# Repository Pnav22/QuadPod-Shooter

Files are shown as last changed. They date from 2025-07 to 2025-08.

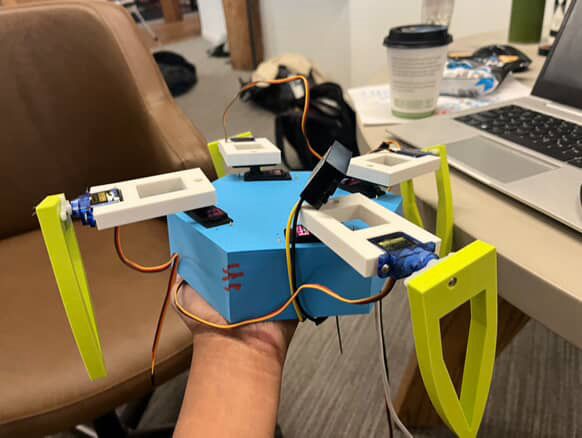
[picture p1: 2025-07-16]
Pictures/WhatsApp Image 2025-07-16 at 11.27.03_aa79fecd.jpg

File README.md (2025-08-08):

# Quadrapod Turret

**Quadrapod Turret** is a four-legged spider-bot equipped with a turret, created for the Hack Club Undercity Hackathon at github. Each leg has two servo motors that enable rotation across two axes, allowing the robot to walk smoothly. The turret features an automatic reloading and firing system. The entire robot is controlled wirelessly via Bluetooth using an Xbox controller.

## Demo Video
 [Watch it here on YouTube](https://www.youtube.com/shorts/YrqL98bALRE)

## Build Journal
We thought we needed a journal even though we didn't, so we made one. Check out our full build log in [`journal.md`](https://github.com/Pnav22/QuadPod-Shooter/blob/main/Journal.md)   

Check out some more pictures in [`Pictures`](https://github.com/Pnav22/QuadPod-Shooter/tree/main/Pictures)

**Creators:** Joel Biswas, Ayush Jaiswal, and Pranav Mukkara

CAD                         |  IRL
:-------------------------:|:-------------------------:
CAD Render  |  IRL Build

---

## Movement Mechanism

The robot has four legs, each with two joints controlled by servo motors:

- **MG996R servo**: Controls one joint axis  
- **SG90 servo**: Controls the other joint axis

Together, these allow each leg to move in two degrees of freedom, enabling the robot to walk with stability and precision.

---

## Turret Mechanism

- Two **N20 DC motors** power the flywheels that launch ammunition.  
- An **SG90 servo motor** controls the reloading mechanism.  
- Ammunition consists of 1 cm spherical pellets loaded in a vertical tube.  
- The servo pushes ammo into the flywheels, which spin at high speed to fire the pellets.

---

## Design

Cad can be viewed [here](https://cad.onshape.com/documents/1f07b48c7f0c844885f208f0/w/35ef43929f689d5c59df734c/e/4c060ffb7e05090ceb09d7bd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).

SpiderCAD

Read Journal.md to see our engineering process!
---

## Bill of Materials

| Item | Quantity |
|---|---|
| SG90 Servo Motor | 5 |
| MG996R Servo | 5 |
| ESP32 DevKit C | 1 |
| Breadboard | 1 |
| Male to Male Jumper Wires | 30 |
| 3S LiPo Battery | 1 |
| 12V to 5V Buck Converter | 1 |
| PLA (kgs) | 1 |
| N20 Motor | 2 |
| XT60 Male Connector | 1 |

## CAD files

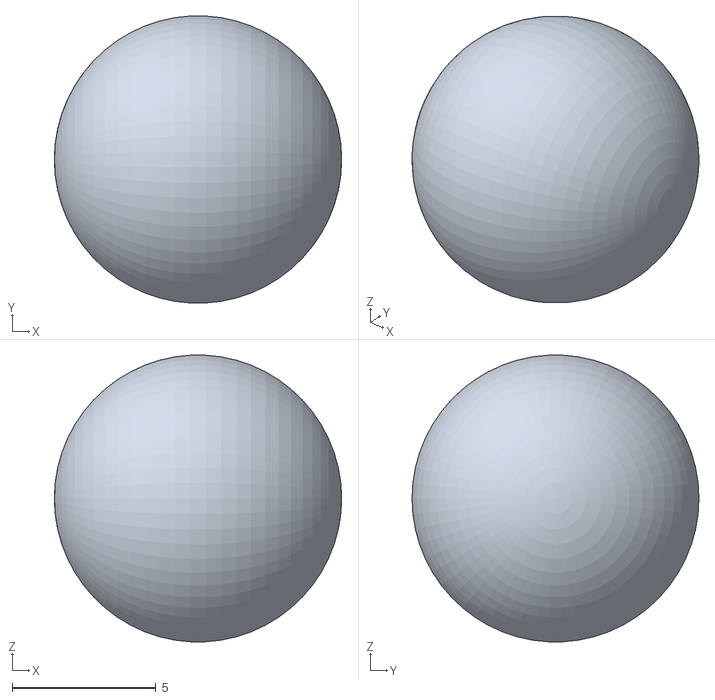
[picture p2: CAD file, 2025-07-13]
CAD/STL Files/Ammo.stl
10.0 x 9.99 x 9.97

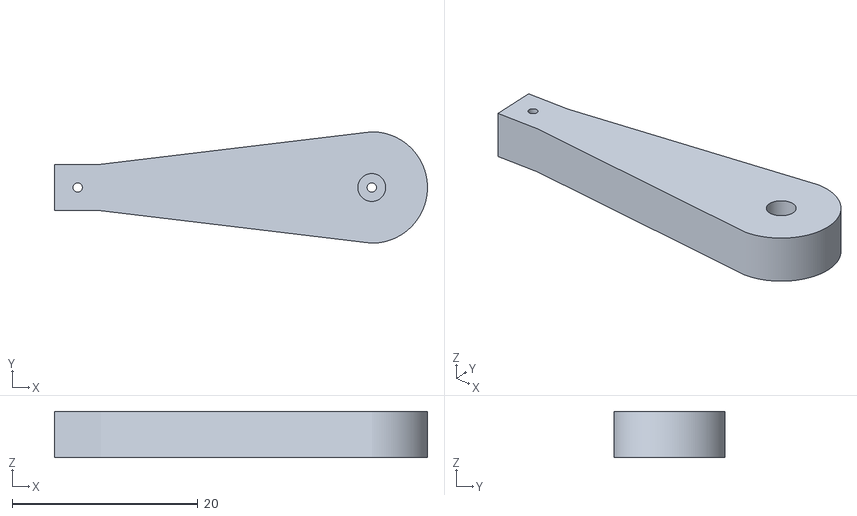
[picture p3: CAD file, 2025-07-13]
CAD/STL Files/Reload Arm.stl
40.2 x 12.0 x 5.00

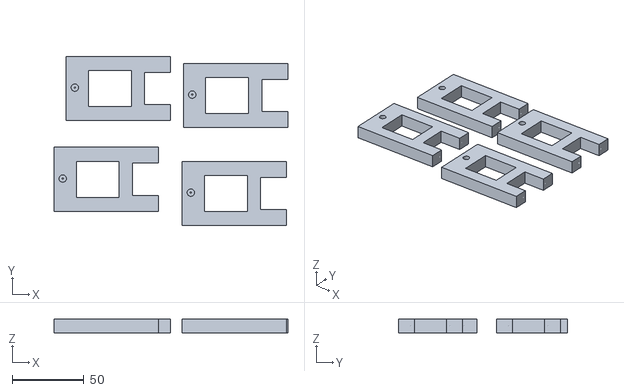
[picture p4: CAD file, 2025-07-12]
Production/legs.stl
163.4 x 118.3 x 10.0

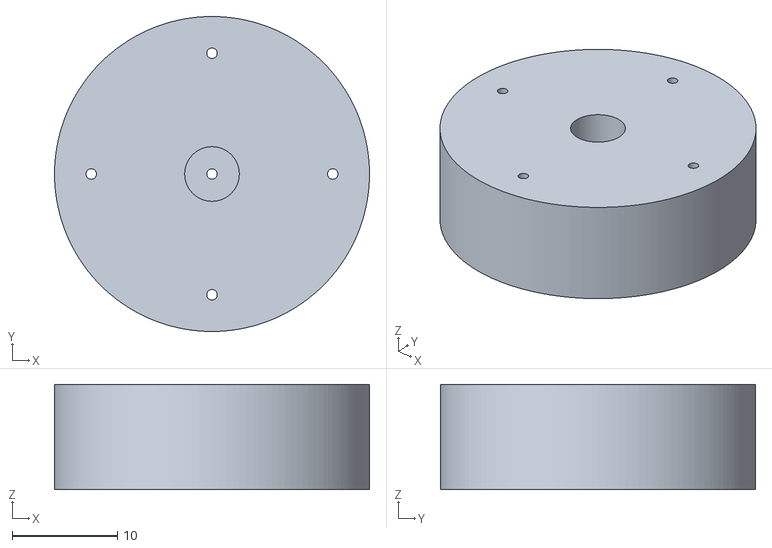
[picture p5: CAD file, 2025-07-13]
CAD/STL Files/Reload Wheel.stl
30.0 x 30.0 x 10.0

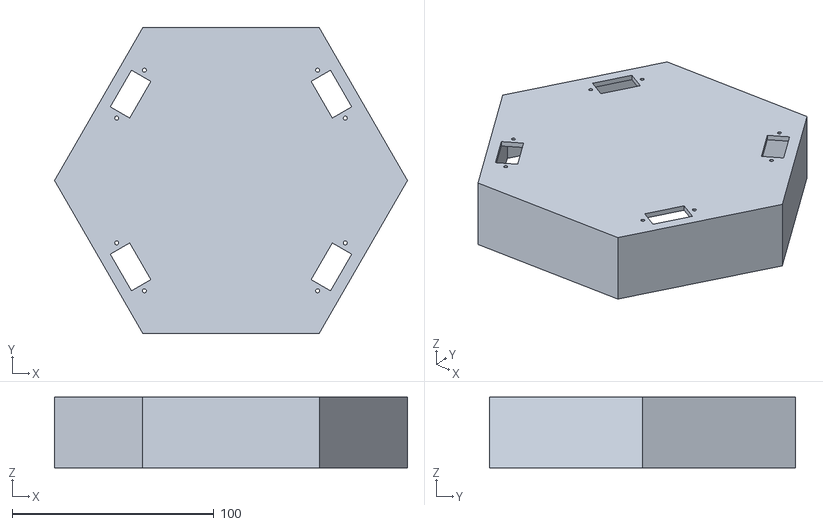
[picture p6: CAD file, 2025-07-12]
Production/Body.stl
175.0 x 151.6 x 35.0

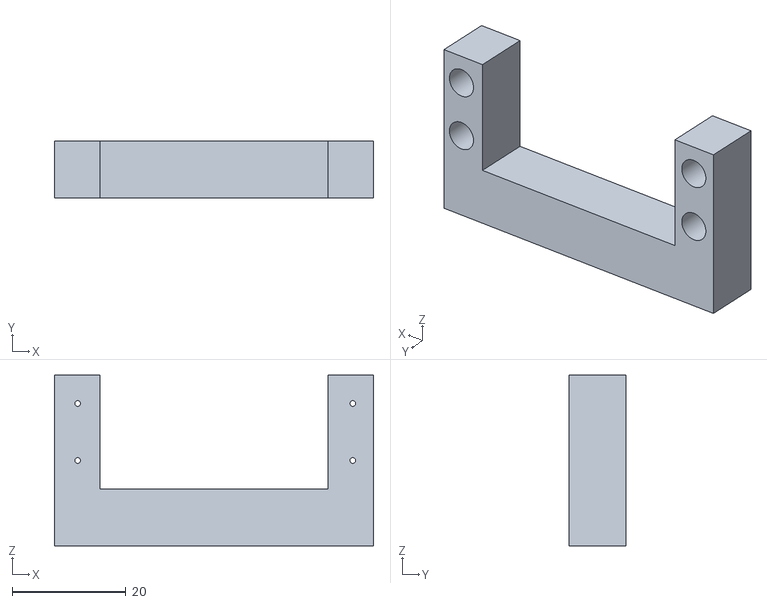
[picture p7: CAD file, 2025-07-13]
CAD/STL Files/Turret Mounting Bracket.stl
56.0 x 10.0 x 30.0

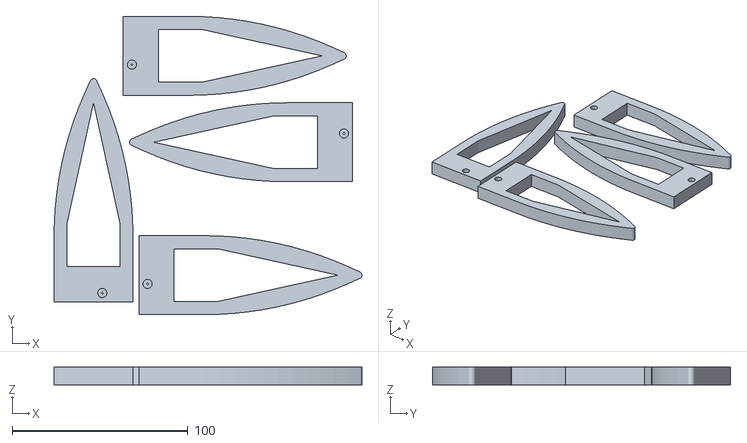
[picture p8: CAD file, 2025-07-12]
Production/claws.stl
175.4 x 169.9 x 10.0

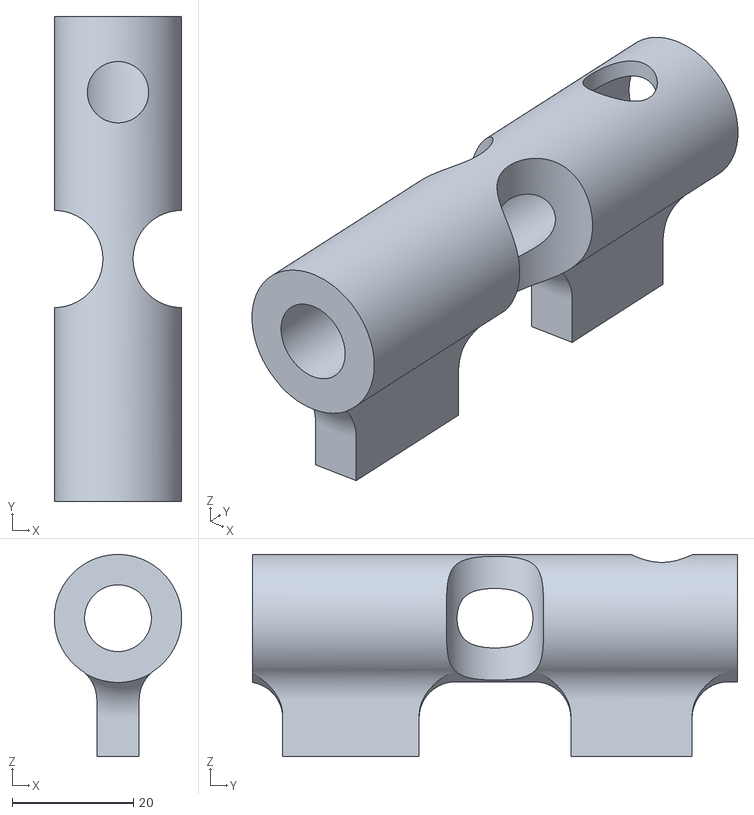
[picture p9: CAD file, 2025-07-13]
CAD/STL Files/Shaft.stl
21.0 x 80.0 x 33.3

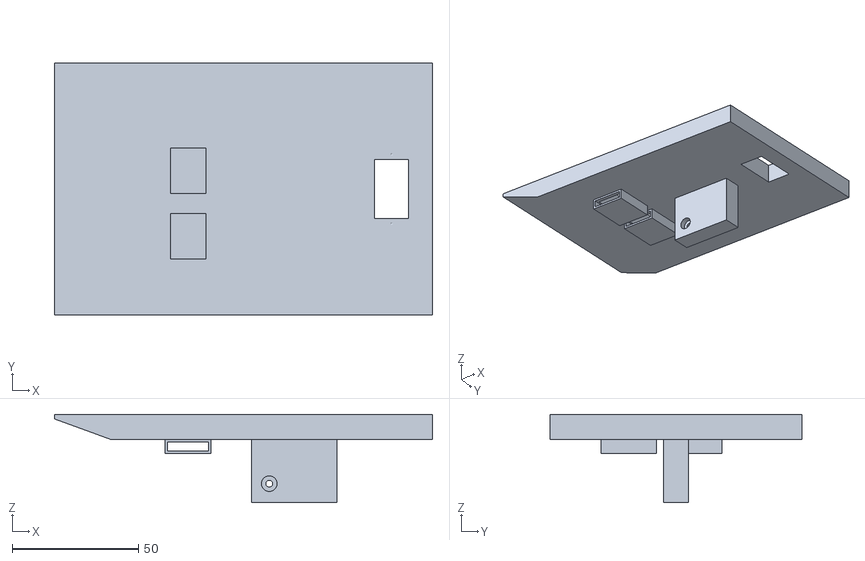
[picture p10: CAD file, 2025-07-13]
CAD/STL Files/Baseplate.stl
150.0 x 100.0 x 35.0

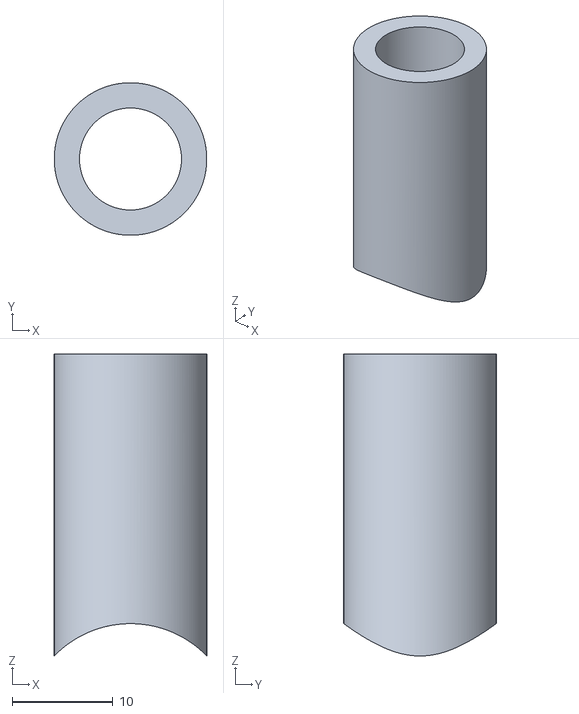
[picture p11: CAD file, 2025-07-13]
CAD/STL Files/Chamber.stl
15.1 x 15.1 x 29.9

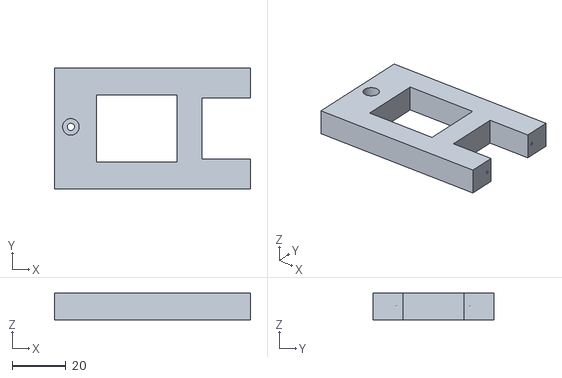
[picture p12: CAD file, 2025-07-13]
CAD/STL Files/Leg X Axis.stl
73.0 x 45.0 x 10.0

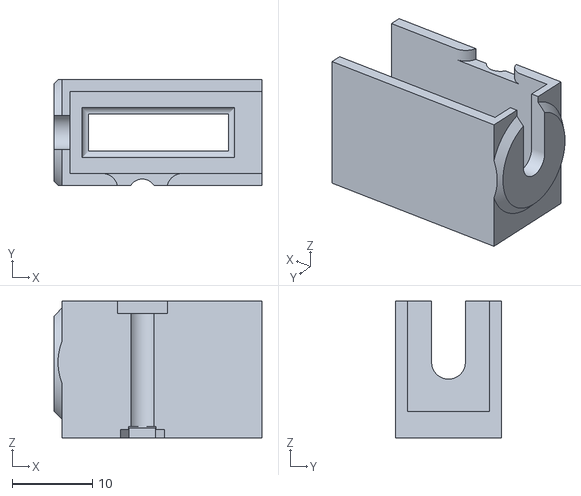
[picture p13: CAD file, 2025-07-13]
CAD/STL Files/Motor Mounts.stl
25.9 x 13.2 x 17.0

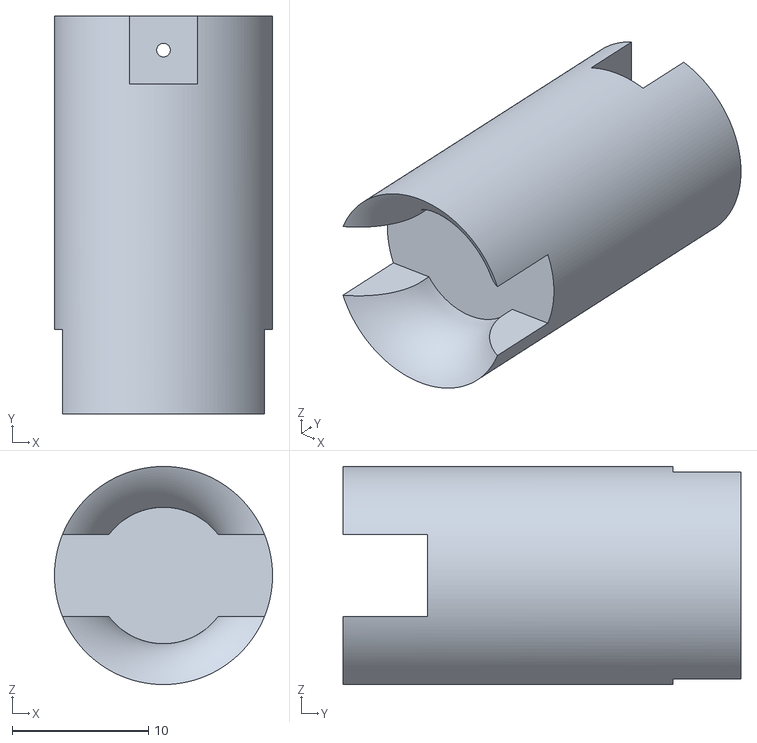
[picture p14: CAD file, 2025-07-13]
CAD/STL Files/Pusher.stl
16.0 x 29.2 x 16.0

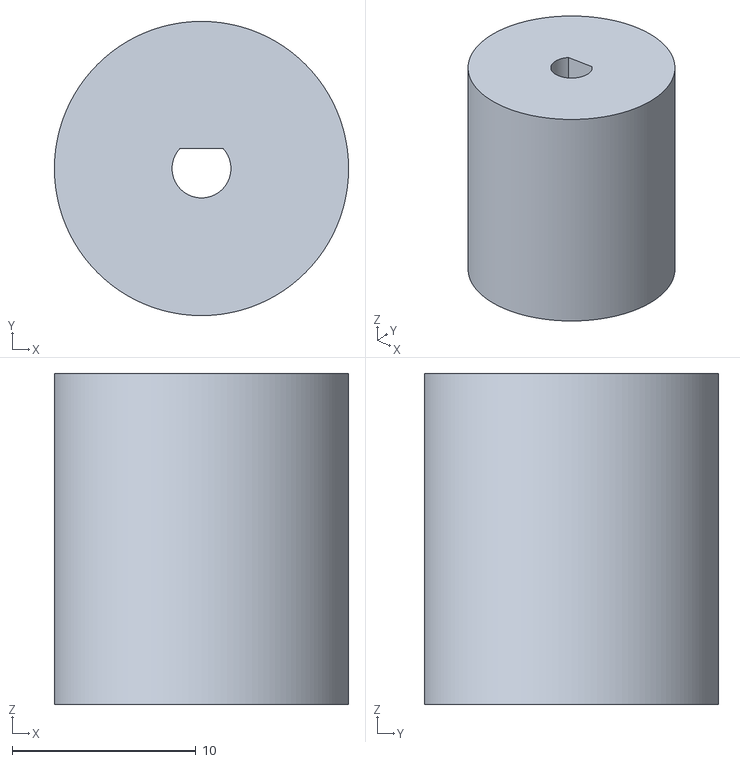
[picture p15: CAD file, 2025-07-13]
CAD/STL Files/Flywheel.stl
16.0 x 16.0 x 18.0

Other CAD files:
Production/Turret.gcode.3mf
CAD/STL Files/Leg Y Axis.stl

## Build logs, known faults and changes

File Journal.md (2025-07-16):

---
title: "QuadPod"
author: "Joel Biswas, Ayush Jaiswal, Pranav Mukkara"
description: "4-Leg Spider Robot"
created_at: "2025-07-11"
---

# QuadPod Build Log

## July 11: Excitement and Exploration

We just arrived at GitHub HQ. The place is amazing—tons of snacks and awesome working spaces. We're super excited to spend the next few nights here for the hackathon.

## July 11: Research and Ideas

We started brainstorming project ideas. One of our first concepts was a drone that acts like a hat—something like this:

Drone Hat Concept

Except this one would actually fly.

Then we explored the idea of a Mark Rober-style hat:

Mark Rober Hat Inspiration

We liked this, but kept brainstorming.

Eventually, we landed on the idea of a six-legged spider robot—something that would make people say, *"That's cool as f***." We found inspiration in this:

Spider Bot Inspiration

To make it even cooler, we decided to mount a Nerf gun on top.

In the end, we scaled it down to four legs to simplify the build.

## July 11 to 12: Getting Started

We began CAD work and created some basic designs:

Initial CAD Progress

We sent the parts out to get printed. One of our biggest mistakes was spending too much time on CAD before securing the parts we needed. By the time we went to grab motors, most were already gone—we were two short.

This was our first major roadblock. We didn’t check part availability before designing. Someone had taken eight of the motors we needed.

We decided to redesign the CAD to work with the motors that were still available.

Eventually, we found the original motors again and reverted to our original CAD design. Shoutout to Alex for coming in clutch with two extra motors from a workshop!





## July 12: Setting Up the ESP32

Pranav stayed up all night trying to get the ESP32 to work. He wanted to start coding but realized the board wasn’t responding.

He tried multiple computers and ESP32s, only to discover hours later that none of the USB cables he had supported data transfer. A whole all-nighter wasted.



The pin guide was also a nightmare. This was our second major roadblock. One person spent the entire night trying to set up the ESP32, only to realize none of the wires available could transfer data.

## July 12: Finalizing the CAD

We finalized the CAD and started printing and assembling. We used screws from the servo motor kits for assembly. Parts were printed and things started coming together.

## July 12: Third Roadblock - Servo Mounting

We messed up the leg brackets. The rectangular mounts that hold the servos had incorrect tolerances—the screws didn’t reach far enough. The servos weren't properly meshed with the arms, so nothing moved when powered.

To fix this, we used a soldering iron to heat-set the screws into the plastic. That way, when the servo moved, the arms moved with it.

## July 13: Fourth Roadblock - Wiring

Wiring was a nightmare. We were up at 4 a.m. redoing all the connections due to GPIO issues. Here’s a photo of the chaos:

WhatsApp Image 2025-07-13 at 15 31 15_a4ac9f2a

## July 13: Assembly

We assembled the entire robot! Here are some photos:

WhatsApp Image 2025-07-13 at 15 06 22_39daa7c8  
WhatsApp Image 2025-07-13 at 15 06 22_d549f691

The team in action:

WhatsApp Image 2025-07-13 at 15 06 22_2a913bad

## July 13: Coding

We're now deep into coding.
## July 14: Event End

This hackathon has ended so we are not working on the project anymore. We had lots of fun!

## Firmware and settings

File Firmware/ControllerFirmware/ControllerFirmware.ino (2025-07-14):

#include <Bluepad32.h>

// Servo objects
constexpr uint8_t legXPin1 = 13; // D13 - X BACK LEFT
constexpr uint8_t legXPin2 = 27; // D27 - X FRONT RIGHT
constexpr uint8_t legXPin3 = 12; // D12 - X BACK RIGHT
constexpr uint8_t legXPin4 = 14; // D14 - X FRONT LEFT

constexpr uint8_t legXChannel1 = 0;
constexpr uint8_t legXChannel2 = 1;
constexpr uint8_t legXChannel3 = 2;
constexpr uint8_t legXChannel4 = 3;

constexpr uint8_t legYPin1 = 26; // D26 - Y BACK LEFT
constexpr uint8_t legYPin2 = 32; // D32 - Y FRONT RIGHT
constexpr uint8_t legYPin3 = 25; // D25 - Y BACK RIGHT
constexpr uint8_t legYPin4 = 33; // D33 - Y FRONT LEFT

constexpr uint8_t legYChannel1 = 4;
constexpr uint8_t legYChannel2 = 5;
constexpr uint8_t legYChannel3 = 6;
constexpr uint8_t legYChannel4 = 7;

// Constants
const int neutral = 90;    // reset position
const int stepAngle = 60;  // how far forward to move
const int moveDelay = 500; // wait time between movements
const int swingAngle = 40;

const int HERTZ = 50;
const uint8_t BYTES = 12;

bool isWalking;

constexpr uint8_t STATUS_LED = 2;
ControllerPtr myControllers[BP32_MAX_GAMEPADS];

void onConnectedController(ControllerPtr ctl)
{
    Serial.println("Controller connected");
    myControllers[0] = ctl;
    digitalWrite(STATUS_LED, HIGH);
    ctl->playDualRumble(0, 500, 255, 128);
}

void onDisconnectedController(ControllerPtr)
{
    Serial.println("Controller disconnected");
    myControllers[0] = nullptr;
    digitalWrite(STATUS_LED, LOW);
}

void processGamepad(ControllerPtr ctl)
{
    if (ctl->a())
    {
        Serial.println("Rick Ross Mongolian Throat Singing");
        Serial.println(isWalking);
        if (!isWalking)
        {
          isWalking = true;
          walk();
        }
    }
}

void setup()
{
    Serial.begin(115200);

    pinMode(STATUS_LED, OUTPUT);
    digitalWrite(STATUS_LED, LOW);

    ledcSetup(legXChannel1, HERTZ, BYTES);
    ledcSetup(legXChannel2, HERTZ, BYTES);
    ledcSetup(legXChannel3, HERTZ, BYTES);
    ledcSetup(legXChannel4, HERTZ, BYTES);

    ledcSetup(legYChannel1, HERTZ, BYTES);
    ledcSetup(legYChannel2, HERTZ, BYTES);
    ledcSetup(legYChannel3, HERTZ, BYTES);
    ledcSetup(legYChannel4, HERTZ, BYTES);

    ledcAttachPin(legXPin1, legXChannel1);
    ledcAttachPin(legXPin2, legXChannel2);
    ledcAttachPin(legXPin3, legXChannel3);
    ledcAttachPin(legXPin4, legXChannel4);

    ledcAttachPin(legYPin1, legYChannel1);
    ledcAttachPin(legYPin2, legYChannel2);
    ledcAttachPin(legYPin3, legYChannel3);
    ledcAttachPin(legYPin4, legYChannel4);

    // All start at neutral position
    writeToServo(legXChannel1, neutral);
    writeToServo(legXChannel2, neutral);
    writeToServo(legXChannel3, neutral);
    writeToServo(legXChannel4, neutral);

    writeToServo(legYChannel1, neutral);
    writeToServo(legYChannel2, neutral);
    writeToServo(legYChannel3, neutral);
    writeToServo(legYChannel4, neutral);
    delay(500);

    isWalking = false;

    BP32.setup(&onConnectedController, &onDisconnectedController);
    // BP32.forgetBluetoothKeys(); PLEASE DO NOT UNCOMMENT THIS
    BP32.enableVirtualDevice(false);
}

void loop()
{
    if (BP32.update())
    {
        ControllerPtr ctl = myControllers[0];
        if (ctl && ctl->isConnected() && ctl->hasData() && ctl->isGamepad())
            processGamepad(ctl);
    }
    delay(10);
}

void writeToServo(int pwmChannel, int angle)
{
    // Map angle (0–180) to pulse width in microseconds (1000–2000)
    int us = map(angle, 0, 180, 1000, 2000);

    // Convert microseconds to duty (out of 2^16 for 16-bit resolution and 50Hz)
    uint32_t duty = (us * 4095UL) / 20000UL; // for 12-bit

    Serial.print("Angle: ");
    Serial.print(angle);
    Serial.print(" → Duty: ");
    Serial.println(duty);

    ledcWrite(pwmChannel, duty);
}


void walk() {
  Serial.println("MIT Library Activities");

  moveLeg(legXChannel1, legYChannel1, + stepAngle); // back left
  moveLeg(legXChannel2, legYChannel2, + stepAngle); // front right
  moveLeg(legXChannel3, legYChannel3, + stepAngle); // back right
  moveLeg(legXChannel4, legYChannel4, + stepAngle); // front left

  isWalking = false;
  Serial.println("Sh*wering?!");
}

void moveLeg(int xChannel, int yChannel, int swingAngle) {
  writeToServo(yChannel, neutral + swingAngle); // lift leg
  delay(moveDelay / 2);
  writeToServo(xChannel, neutral + swingAngle);
  delay(moveDelay);
  writeToServo(yChannel, neutral);
  delay(moveDelay / 2);
  writeToServo(xChannel, neutral);
  delay(moveDelay);
}

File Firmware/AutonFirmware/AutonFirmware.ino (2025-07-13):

#include <ESP32Servo.h>

// Create servo objects
Servo Xleg1;  // D13 - back left
Servo Xleg2;  // D27 - front right
Servo Xleg3;  // D12 - back right
Servo Xleg4;  // D14 - front left

// Constants
const int neutral = 90;
const int stepAngle = 30;     // how far to swing
const int moveDelay = 500;    // ms between each move

void setup() {
  Serial.begin(115200);
  Serial.println("Starting walk test...");

  // Attach servos
  Xleg1.setPeriodHertz(50); Xleg1.attach(13);
  Xleg2.setPeriodHertz(50); Xleg2.attach(27);
  Xleg3.setPeriodHertz(50); Xleg3.attach(12);
  Xleg4.setPeriodHertz(50); Xleg4.attach(14);

  // Start in neutral
  Xleg1.write(neutral);
  Xleg2.write(neutral);
  Xleg3.write(neutral);
  Xleg4.write(neutral);
  delay(1000);

  // Run the test walk sequence
  for (int i = 0; i < 2; i++) {
    Serial.print("Cycle "); Serial.println(i + 1);

    // 13f
    Xleg1.write(neutral + stepAngle);
    delay(moveDelay);

    // 27f
    Xleg2.write(neutral + stepAngle);
    delay(moveDelay);

    // 12f
    Xleg3.write(neutral + stepAngle);
    delay(moveDelay);

    // 13r
    Xleg1.write(neutral);
    delay(moveDelay);

    // 14f
    Xleg4.write(neutral + stepAngle);
    delay(moveDelay);

    // 27r
    Xleg2.write(neutral);
    delay(moveDelay);

    // 12r
    Xleg3.write(neutral);
    delay(moveDelay);

    // 14r
    Xleg4.write(neutral);
    delay(moveDelay);
  }

  Serial.println("Test complete!");
}

void loop() {
  // Do nothing, keep servos in place
}

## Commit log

2025-07-12 Added Body STL
    [SpideyBody.stl]
2025-07-12 NEW STL FILES
    [Body.stl, Leg X Axis.stl, Leg Y Axis.stl]
2025-07-12 STL Updated
    [Leg X Axis.stl, Leg Y Axis.stl]
2025-07-12 Deleted Old Body
    [SpideyBody.stl]
2025-07-12 Updated Body.stl
    [Body.stl]
2025-07-12 Updateed Leg X Axis
    [Leg X Axis.stl]
2025-07-13 New STLs
    [Flywheel.stl, Motor Mounts.stl, Pusher.stl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]
2025-07-13 Shaft STL
    [Shaft + Chamber + Supports.stl]
2025-07-13 Added Turret
    [Ammo.stl, Turret.gcode.3mf]
2025-07-13 Updated baseplate
    [Baseplate.3mf]
2025-07-13 Added BOM
    [Ammo.stl, BOM.csv, Baseplate.3mf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]
